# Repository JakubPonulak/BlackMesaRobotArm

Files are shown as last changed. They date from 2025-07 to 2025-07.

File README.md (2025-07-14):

<p align="center">
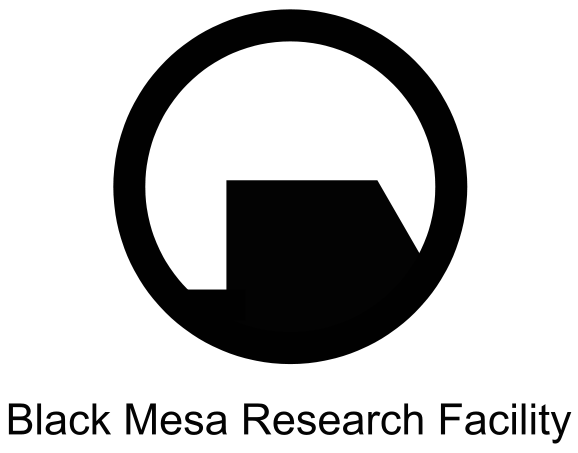
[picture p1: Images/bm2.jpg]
  
</p>

# Black Mesa Robot Arm
This is the GitHub repository for the Black Mesa Hazardous Material Manipulation Device, a small robot arm powered by an Arduino Uno microcontroller, which can be operated through keyboard inputs via Bluetooth. The purpose of this project was to utilize my knowledge of mechanical, electrical, and software engineering into a working device with a practical purpose.

<p align="center">
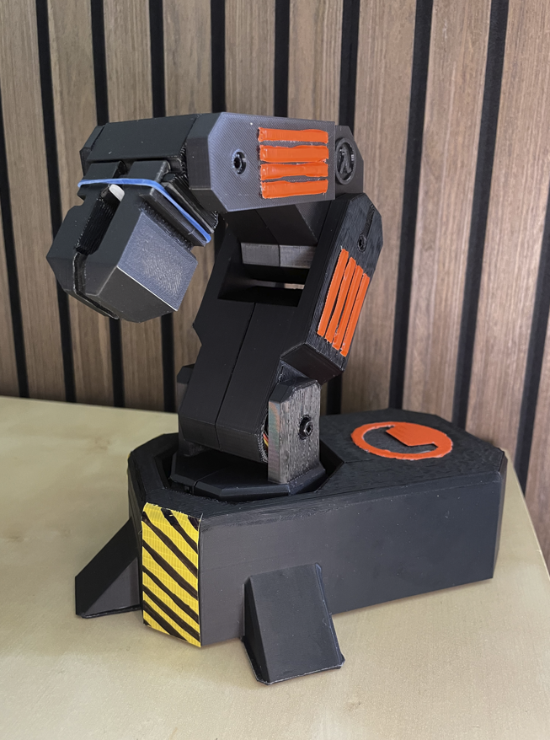
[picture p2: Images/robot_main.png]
  
</p>

The name of the robot, along with its design and decorative elements, come from the iconic video game "Half-Life", which was groundbreaking at the time of its release and has heavily impacted the FPS genre. Specifically, the robot name and design are a reference to the Black Mesa Research Facility, a fictional laboratory complex and research center which is the setting of the game. This game is a personal favorite of mine, and its aesthetic and theme fit perfectly into this project.

## Table of Contents

- [Initial Design](#initial-design)
- [Writing Code in Arduino Language and Python](#writing-code-in-arduino-language-and-python)
- [Final Assembly and Wiring](#final-assembly-and-wiring)
- [Do It Yourself!](#do-it-yourself)
- [Conclusion](#conclusion)

## Initial Design
I was first inspired to make this robot arm after watching [this video](https://www.youtube.com/watch?v=5toNqaGsGYs&list=PLPR41m1Dqd8Jqq6F-DI4-8zMKgnmrkHdz) by Build Some Stuff on YouTube. While the robot in the video was interesting on its own, I was determined to make my own version, both in terms of design and how it was to be controlled. I first got to work in Blender, a 3D modelling program that I have been using since high school, and I created a rough "sketch" of what I wanted my robot arm to look like:

<p align="center">
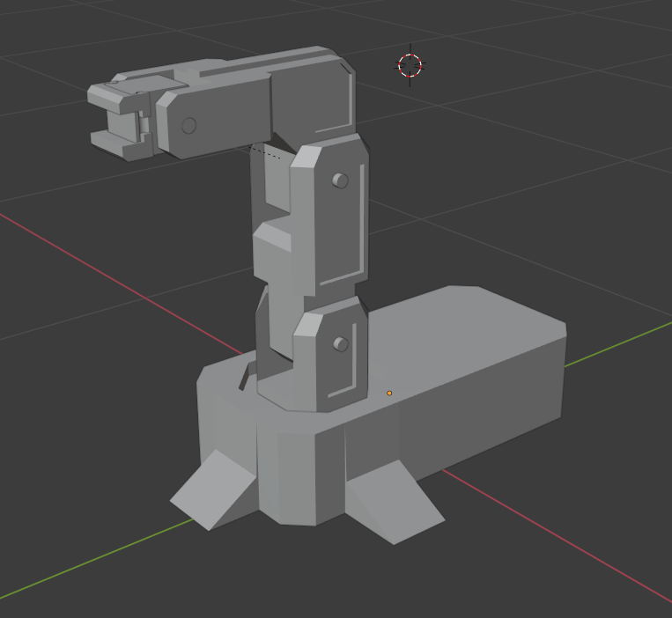
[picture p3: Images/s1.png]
  
</p>

After coming up with this design, I switched over to CAD modeling in SOLIDWORKS, which is better suited for creating real-life components, and with which I have much more experience. Based on dimensions given in the YouTube video's description, I was able to model each individual part of the robot and combine them into a complete SOLIDWORKS assembly, simulating the look and behavior of the robot arm. By importing additional pre-made parts such as Servo Motors and the Arduino Uno, I was able to ensure that the internal components of the robot would fit inside it, and that there were no interferences between components. 

DISCLAIMER: The assembly file that I have uploaded to this repository is a minimal version that can be built using only the parts I created. Please contact me if you would like a complete version that includes these additional parts.

<p align="center">
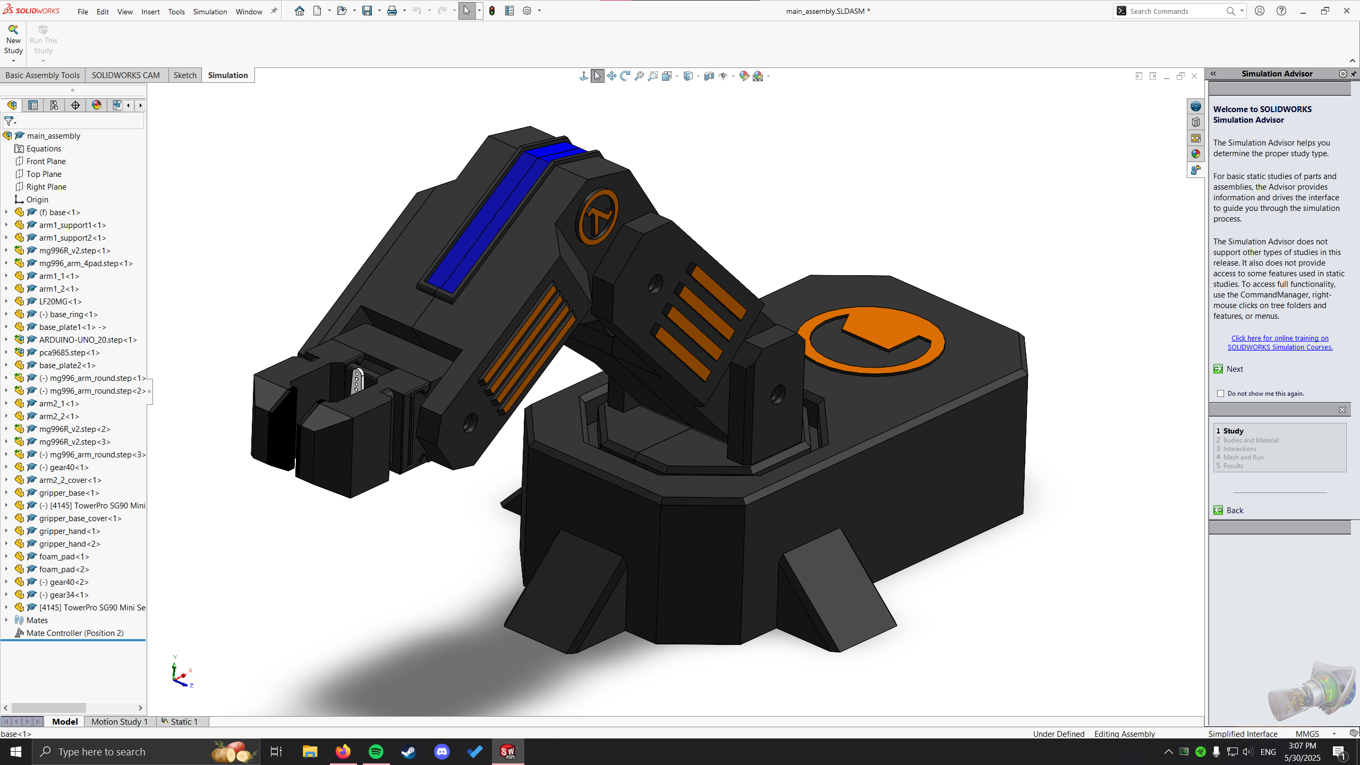
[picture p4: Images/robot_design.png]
  
</p>

Using SOLIDWORKS also allowed me to run an FEA simulation of the robot arm, specifically to see how the arm would react to a 300 gram object being held in place by the grippers, which is the maximum weight that I envisioned the robot would be able to carry with its limited grasp. I ran this simulation multiple times, varying the orientation of the arm in each run. The most critical iteration occurred when the arm was fully outstretched to the side, as this configuration exerted the greatest moment on the base.

<p align="center">
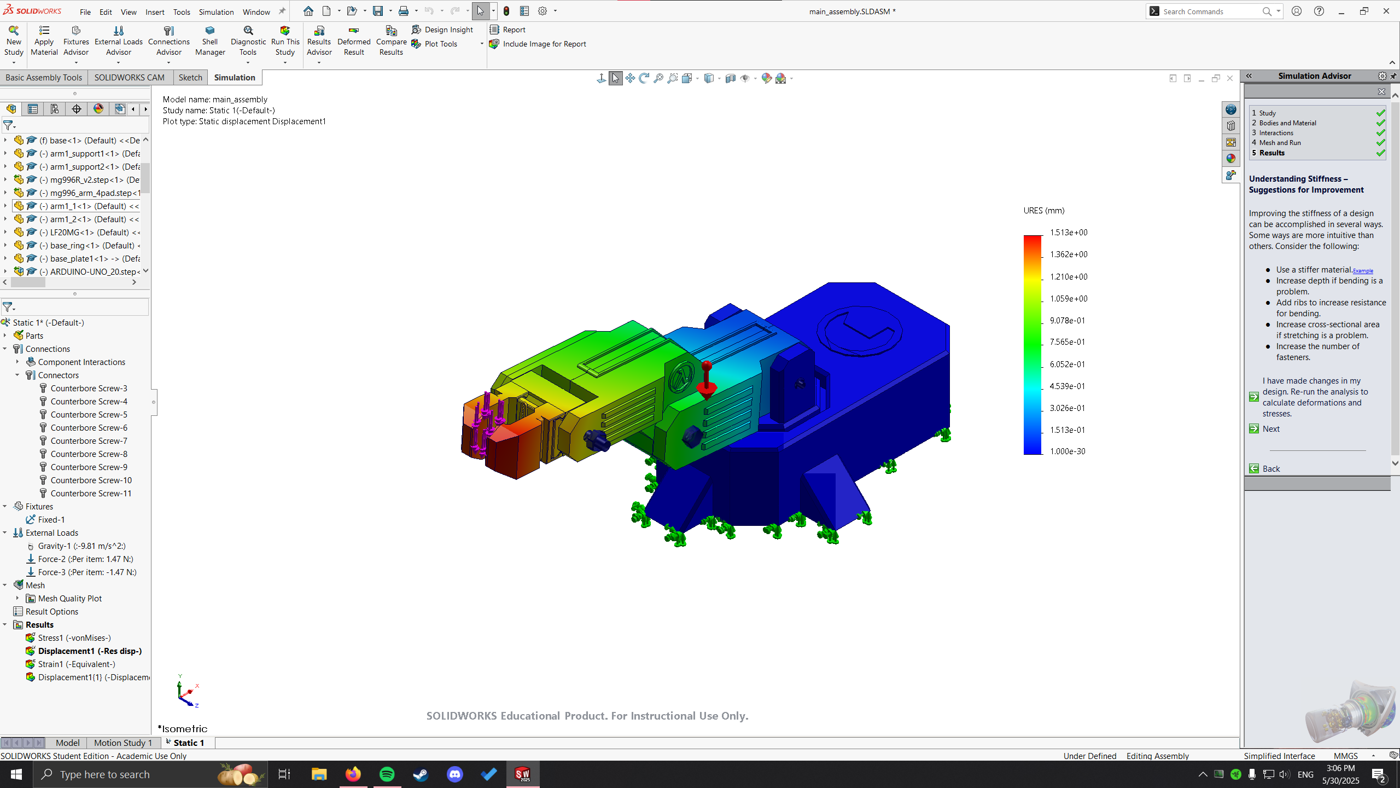
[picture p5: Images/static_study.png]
  
</p>

Once the design was complete, I uploaded my STP files to Craftcloud, an online 3D printing service that matches customers to manufacturers across the globe. While I waited for my parts to be printed in PLA and shipped to my home, I got to work on the software needed to run this robot arm.

## Writing Code in Arduino Language and Python
I had worked with Arduino boards and the Arduino language (a derivative of C++) in the past, and so I was already familiar with writing code for my microcontroller board. However, I had never worked with servo motors before, and so I had to learn about operating and manipulating them, which is where the Adafruit PWM Servo Driver Library comes in. This library allows easy manipulation of servo motors that are connected to the Arduino via a Servo Motor Driver board, which in my case was the PCA9685. I also utilized the EEPROM (Electrically Erasable Programmable Read-Only Memory) library, which allows the program to save data to the Arduino’s built-in non-volatile memory. This makes it possible to store servo positions or settings that are automatically restored when the robot is powered back on.

Initially, I thought that I would only need to write code in the Arduino IDE, but I soon realized that it did not allow for the type of user input I wanted. My initial plan was to control the robot using individual keystrokes like "A", "D", or "Space". However, the Arduino IDE lacked built-in functionality for detecting keyboard input. To work around this, I decided to use Python, which allowed me to use the _keyboard_ library, which allows scripts to detect and respond to keyboard input in real-time. The script reads the user's input on the keyboard, and sends a corresponding signal (a single integer or character) to the Arduino via the appropriate serial port. On the Arduino side, the uploaded code reads the incoming serial data and interprets the command by executing a predefined action, mainly changing the position of a specific servo motor. This setup allows real-time control of the robot arm through simple keystrokes on the keyboard.

## Final Assembly and Wiring
Once all of my 3D-printed parts and mechanical / electrical components arrived in the mail, I was ready to assemble the robot arm. Although the robot was designed with precision in SOLIDWORKS, the physical parts required several adjustments during assembly due to manufacturing imperfections. This included sanding down certain surfaces for a better fit, enlarging holes to properly accommodate screw diameters, and filing edges to improve joint mobility and rotation smoothness.

There were also some design flaws that I had failed to notice when first designing the parts for the robot arm. For example, some of the parts of the robot have cutouts for the servo motor wires, and I had underestimated how much space these wires would take up, especially at the base of the arm, where 4 sets of wires had to squeeze through a small opening. I ended up enlarging this cutout with a cordless drill, and I made sure to adjust the CAD file to match this adjustment if I was ever to reprint that specific part in the future. 

<p align="center">
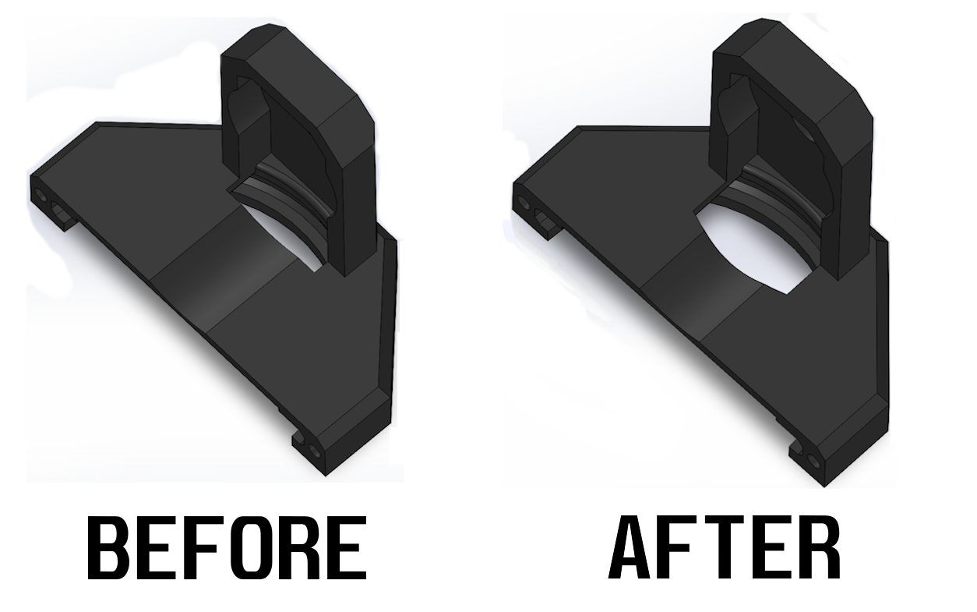
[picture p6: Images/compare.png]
  
</p>

Once the physical components were assembled, I moved on to wiring. I was fortunate to find online guides detailing how to wire the PCA9685 to the Arduino, as well as instructions for connecting the HC-05 Bluetooth module, which required a simple voltage divider that I assembled on a compact breadboard. However, during my first test, I encountered a major problem. Due to the limited space in the robot arm’s base, a short circuit occurred between the On/Off switch and the PCA9685 board. This short damaged the main ground wire and destroyed the female DC power adapter that connected the arm to my power supply. After a lot of troubleshooting and rewiring, I managed to resolve these issues, and the robot arm finally operated as intended. Below is a video of the robot arm in action (click the image to access the link).

<p align="center">
  <a href="https://drive.google.com/file/d/1IjUJEja0Yv61JHg0KjAD3Q2Ghb71W-9r/view?usp=sharing">
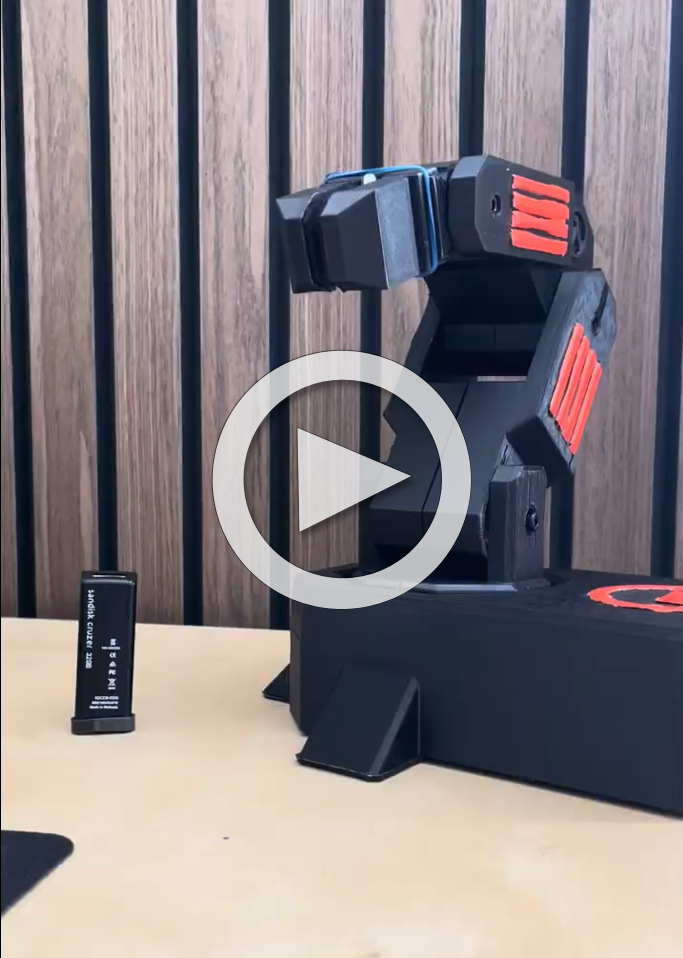
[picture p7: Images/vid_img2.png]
    
  </a>
</p>

## Do It Yourself!
One of the great things about this project is how easy it is to set up. All the necessary components can be ordered online, and the required software is free to download, except for SOLIDWORKS, which requires a paid subscription. However, there are great free alternatives, such as FreeCAD or Onshape. All the files provided in this repository are available for download, so you can use them as-is or modify them as a starting point for your own project. Below is a list of additional materials and parts you’ll need:

### Bill of Materials
#### Servos
- Main Servos: [Link](https://amzn.to/45xkgPH)
- 20KG Servo: [Link](https://amzn.to/43sGe4c)
- Micro Servo: [Link](https://amzn.to/3N3g3fj)
#### Electronics
- Arduino Board: [Link](https://amzn.to/3qfOmHg)
- Servo Driver Board: [Link](https://amzn.to/3spBGz1)
- HC-05 Bluetooth Module: [Link](https://www.amazon.com/Wireless-Bluetooth-Receiver-Transceiver-Transmitter/dp/B01MQKX7VP)
- Adjustable Power Supply: [Link](https://amzn.to/46e27Xa)
#### Hardware
- Screws Larger Set: [Link](https://amzn.to/3C47ASK)
- Screws Small Set: [Link](https://amzn.to/44GC2ih)
- Dupont Connector Kit: [Link](https://amzn.to/3qiVMth)
- T-Plugs: [Link](https://amzn.to/47df3g6)
- Wire/Shrink Wrap: [Link](https://amzn.to/3G3DEYU)
- Mini Breadboard Set: [Link](https://www.amazon.com/WWZMDiB-SYB-170-Breadboard-Plates-Multicolored/dp/B09YXQJMTG)
- Resistor Kit: [Link](https://www.amazon.com/Resistor-Resistors-Assortment-Breadboard-Electronics/dp/B0F4P352BB)
- USB-A Cable: [Link](https://www.amazon.com/dp/B00NH11KIK)
#### Other
- Gripper Gears: [Link](https://amzn.to/42eLIyz)
- Rubber Band: [Link](https://amzn.to/3so2O1n)
- Gripper Foam Pad: [Link](https://amzn.to/3SCE8wA)
- Power Switch: [Link](https://amzn.to/3und1LK)

Once you have all the components, 3D-printed parts, and the necessary code files downloaded, you’re ready to assemble and set up your own robot arm.

### Setup
1. Download the Arduino IDE and load robot_arm.ino: [Link](https://docs.arduino.cc/software/ide-v2/tutorials/getting-started/ide-v2-downloading-and-installing/)
2. Download and set up Python on your computer: [Link](https://www.python.org/downloads/)
3. Install the required Python libraries with this command: pip install pyserial keyboard
4. Follow the instructions in [these videos](https://www.youtube.com/watch?v=5toNqaGsGYs&list=PLPR41m1Dqd8Jqq6F-DI4-8zMKgnmrkHdz), made by the original creator Build Some Stuff on YouTube. Ignore the sections about the potentiometer controls.
5. Set up the HC-05 Bluetooth Module using the following wiring diagram:

<p align="center">
  
</p>

**Important Note**: Both the PCA9685 servo driver and the HC-05 Bluetooth module require a 5V power supply, and the Arduino Uno only has one 5V output pin. To power both modules at the same time, you’ll need to use a breadboard or a splitter to distribute the 5V line from the Arduino to both the PCA9685 and the HC-05. Be sure to also connect their grounds (GND) together with the Arduino’s GND to ensure a common reference voltage. 

5. Plug the USB-A cable into your robot and computer. This is how you will upload your code to the Arduino Uno itself.
6. Unplug the RX and TX wires (green and blue in the diagram) from the Arduino, as we cannot upload the code while they are connected.
7. Upload the Arduino code to the microcontroller in the Arduino IDE, then unplug the USB-A cable and reconnect the RX and TX wires.
8. Power on the robot by plugging in the T-Plug, setting your adjustable power supply to 6.0 V.
10. Pair the HC-05 Bluetooth module with your computer via Bluetooth. When prompted for a PIN, use the default code, which is typically 0000 or 1234.
11. Check what COM port the HC-05 is using in your computer's Device Manager, then update robot_arm.py to match it.
12. Run the robot_arm.py script and start controlling your robot arm with your keyboard!

## Conclusion
This project gave me the opportunity to apply my engineering knowledge in a practical setting while exposing me to real-world challenges that engineers face daily. It allowed me to develop my mechanical, electrical, and software skills in a hands-on and rewarding way. I highly recommend this type of project to anyone passionate about Mechanical Engineering who wants to gain valuable, multidisciplinary experience.

This project is licensed under the MIT License, which allows anyone to use, modify, and share the content, provided they give proper credit to the original author.

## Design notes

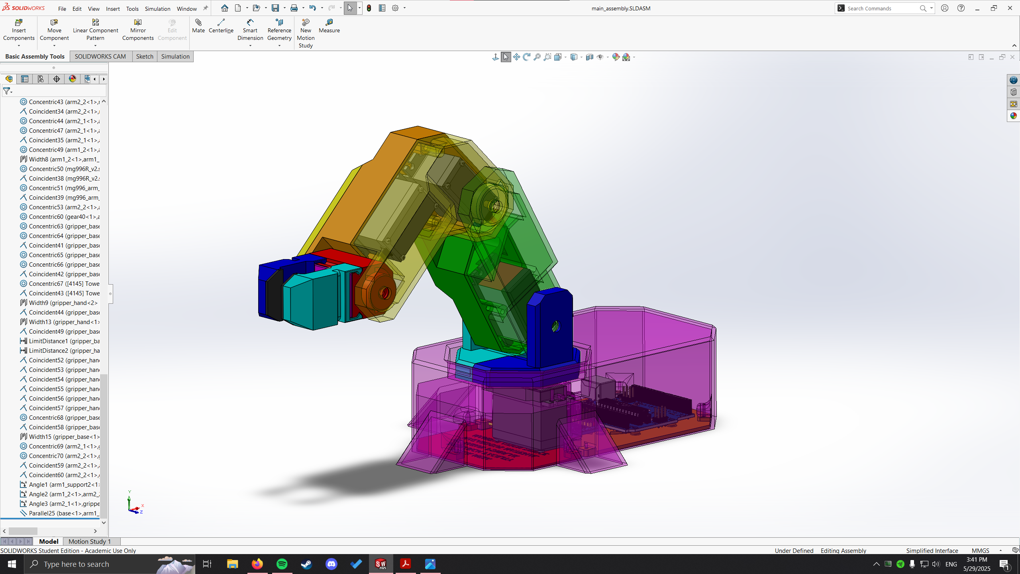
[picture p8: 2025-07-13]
Images/robot_complete.png

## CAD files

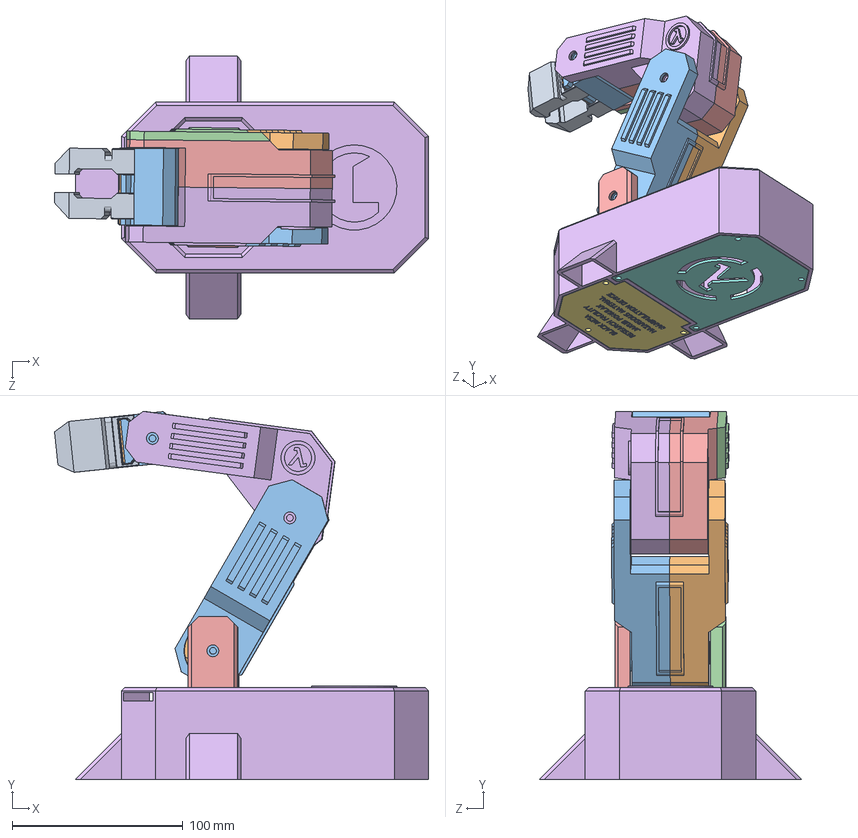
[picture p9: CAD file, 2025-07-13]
CAD Files/main_assembly_min.SLDASM
219.2 x 215.8 x 154.0 mm
base
arm1_support1
arm1_support2
arm1_1
arm1_2
base_ring
base_plate1
base_plate2
arm2_1
arm2_2
arm2_2_cover
gripper_base
gripper_base_cover
gripper_hand x 2

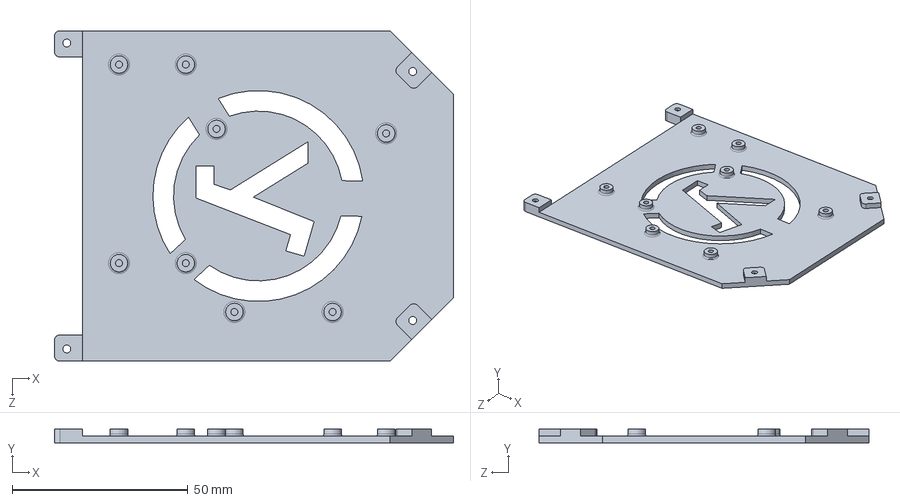
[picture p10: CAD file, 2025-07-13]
CAD Files/base_plate1.SLDPRT
113.5 x 4.00 x 94.0 mm

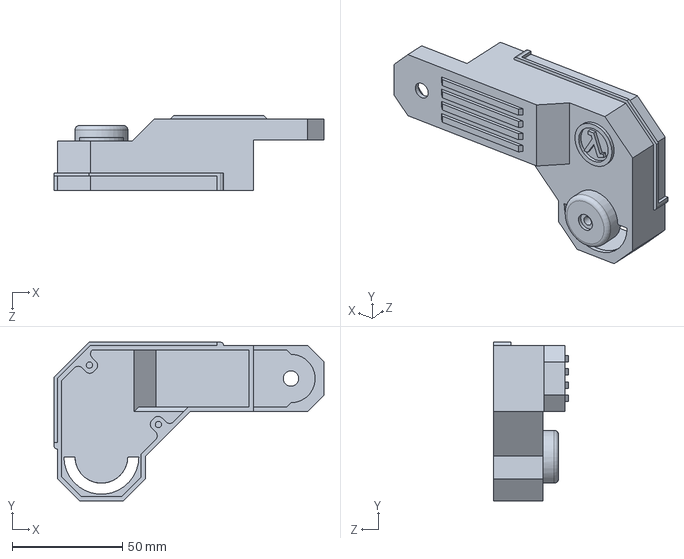
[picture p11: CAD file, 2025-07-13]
CAD Files/arm2_1.SLDPRT
122.5 x 72.0 x 34.0 mm

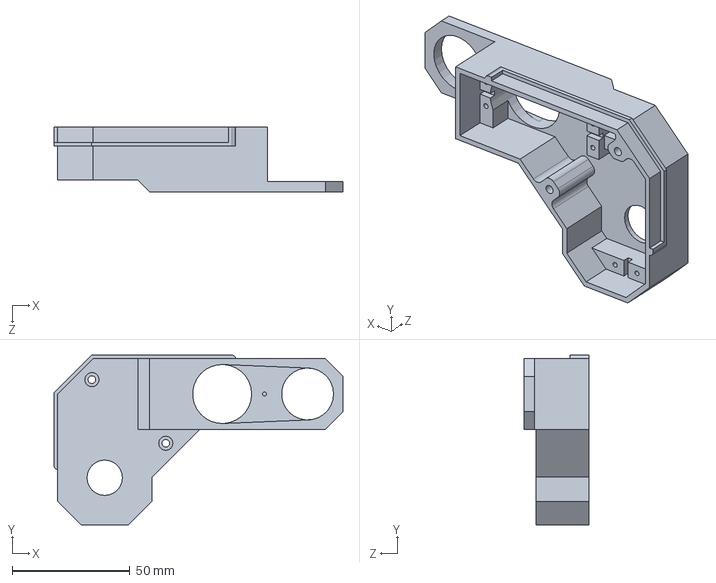
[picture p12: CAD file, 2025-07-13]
CAD Files/arm2_2.SLDPRT
122.5 x 72.0 x 27.5 mm

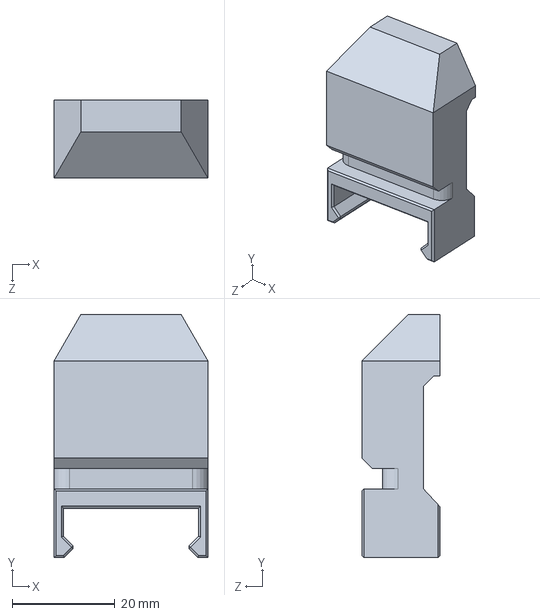
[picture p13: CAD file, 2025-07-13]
CAD Files/gripper_hand.SLDPRT
30.0 x 47.4 x 15.2 mm

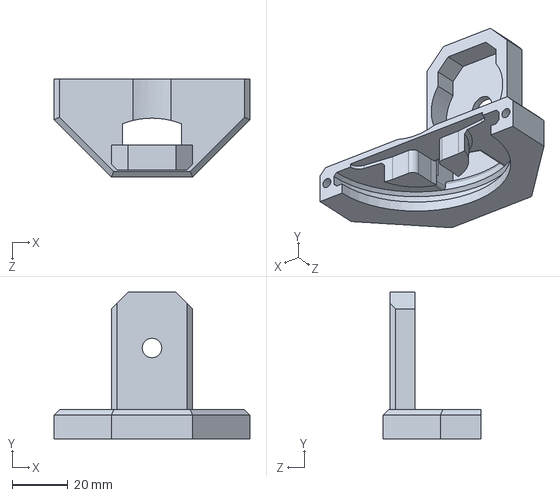
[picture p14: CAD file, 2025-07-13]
CAD Files/arm1_support1.SLDPRT
70.0 x 52.5 x 35.0 mm

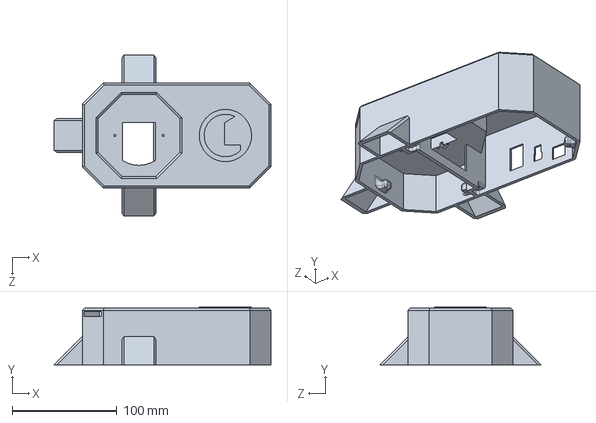
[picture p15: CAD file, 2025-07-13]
CAD Files/base.SLDPRT
207.0 x 55.0 x 154.0 mm

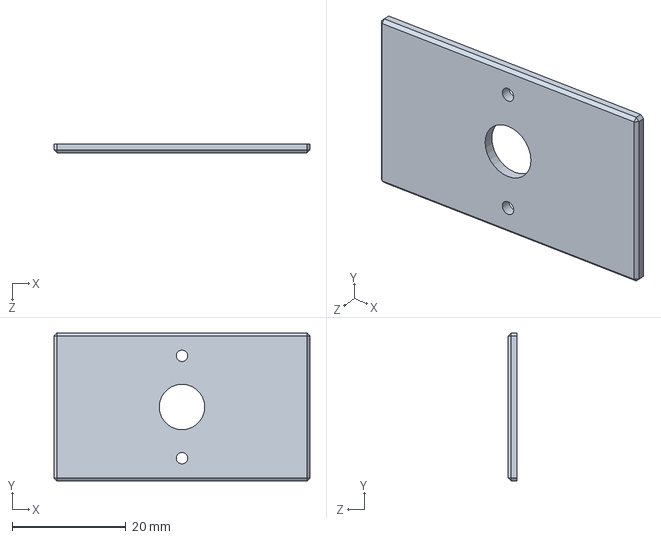
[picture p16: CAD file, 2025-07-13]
CAD Files/gripper_base_cover.SLDPRT
45.0 x 26.0 x 1.50 mm

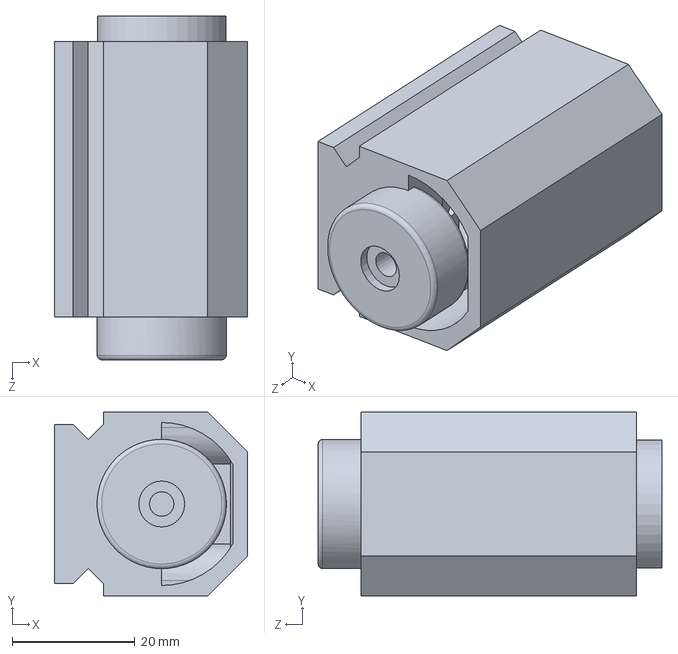
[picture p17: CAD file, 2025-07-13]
CAD Files/gripper_base.SLDPRT
31.5 x 30.0 x 56.1 mm

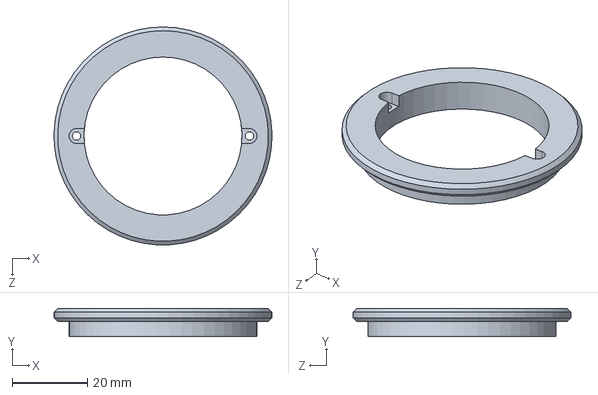
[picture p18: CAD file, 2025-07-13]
CAD Files/base_ring.SLDPRT
58.0 x 7.50 x 58.0 mm

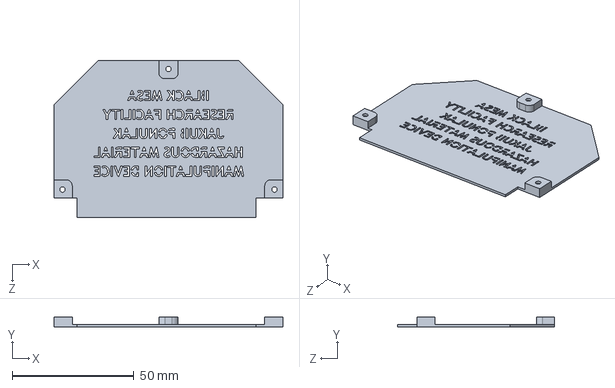
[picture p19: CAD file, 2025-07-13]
CAD Files/base_plate2.SLDPRT
94.0 x 4.00 x 64.5 mm

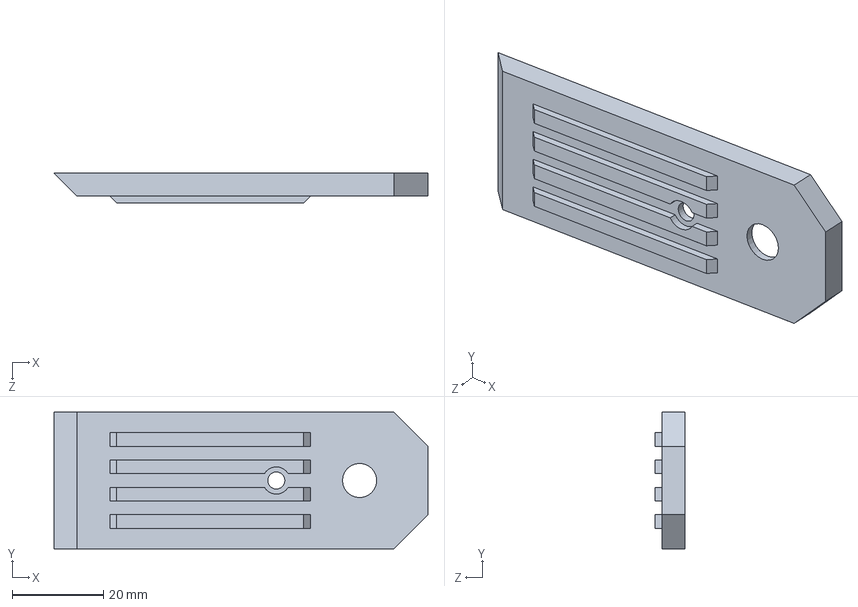
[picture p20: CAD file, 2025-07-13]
CAD Files/arm2_2_cover.SLDPRT
82.0 x 30.0 x 6.50 mm

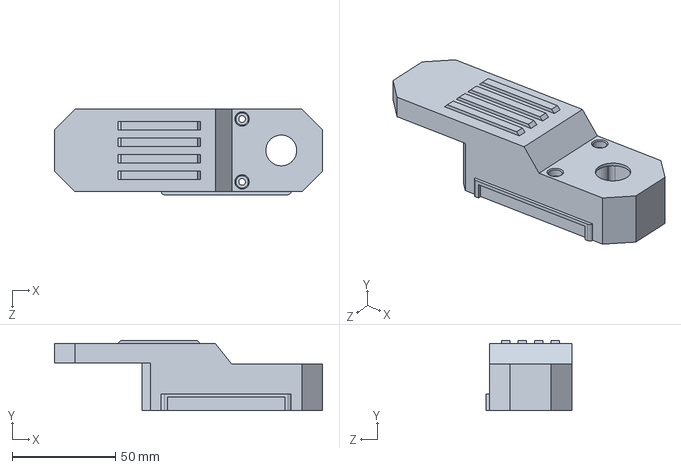
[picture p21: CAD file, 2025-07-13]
CAD Files/arm1_2.SLDPRT
130.0 x 34.0 x 41.5 mm

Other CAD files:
CAD Files/arm1_support2.SLDPRT
CAD Files/arm1_1.SLDPRT

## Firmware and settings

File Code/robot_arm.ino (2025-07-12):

#include <Wire.h>
#include <EEPROM.h>
#include <Adafruit_PWMServoDriver.h>

#define servoMin 75
#define servoMax 535
#define handMin 305
#define handMax 415

Adafruit_PWMServoDriver pwm = Adafruit_PWMServoDriver();  // REMEMBER TO SET VOLTAGE TO 6.00 V

int hand = 11;
int wrist = 10;
int elbow = 9;  //Assign Motors to pins on Servo Driver Board
int shoulder = 7;
int base = 5;

int pos1 = 305;  // hand
int pos2 = 305;  // wrist
int pos3 = 305;  // elbow                // 305 is intermediate value, "middle" of servo
int pos4 = 305;  // shoulder
int pos5 = 305;  // base

const int step = 5;  // step for servo movement per keypress

void setup() {
  Serial.begin(9600);
  pwm.begin();
  pwm.setPWMFreq(50);  // set frequency to 50 Hz
  EEPROM.get(0, pos1);
  EEPROM.get(2, pos2);
  EEPROM.get(4, pos3);
  EEPROM.get(6, pos4);
  EEPROM.get(8, pos5);
  pwm.setPWM(hand, 0, pos1);
  pwm.setPWM(wrist, 0, pos2);
  pwm.setPWM(elbow, 0, pos3);
  pwm.setPWM(shoulder, 0, pos4);
  pwm.setPWM(base, 0, pos5);
}

void loop() {
  if (Serial.available() > 0) {
    char cmd = Serial.read();
    // hand movement
    if (cmd == '4') {
      pos1 += step;
      if (pos1 > handMax) pos1 = handMax;
      pwm.setPWM(hand, 0, pos1);
      Serial.print("Hand opening. Position: ");
      Serial.println(pos1);
    } else if (cmd == '5') {
      pos1 -= step;
      if (pos1 < handMin) pos1 = handMin;
      pwm.setPWM(hand, 0, pos1);
      Serial.print("Hand closing. Position: ");
      Serial.println(pos1);
    }
    // wrist movement
    else if (cmd == '6') {
      pos2 += step;
      if (pos2 > servoMax - 35) pos2 = servoMax - 35;
      pwm.setPWM(wrist, 0, pos2);
      Serial.print("Wrist moving up. Position: ");
      Serial.println(pos2);
    } else if (cmd == '7') {
      pos2 -= step;
      if (pos2 < servoMin + 35) pos2 = servoMin + 35;
      pwm.setPWM(wrist, 0, pos2);
      Serial.print("Wrist moving down. Position: ");
      Serial.println(pos2);
    }
    // elbow movement
    else if (cmd == '8') {
      pos3 += step;
      if (pos3 > servoMax) pos3 = servoMax;
      pwm.setPWM(elbow, 0, pos3);
      Serial.print("Elbow moving down. Position: ");
      Serial.println(pos3);
    } else if (cmd == '9') {
      pos3 -= step;
      if (pos3 < servoMin) pos3 = servoMin;
      pwm.setPWM(elbow, 0, pos3);
      Serial.print("Elbow moving up. Position: ");
      Serial.println(pos3);
    }
    // shoulder movement
    else if (cmd == '3') {
      pos4 += step;
      if (pos4 > servoMax) pos4 = servoMax;
      pwm.setPWM(shoulder, 0, pos4);
      Serial.print("Shoulder moving down. Position: ");
      Serial.println(pos4);
    } else if (cmd == '2') {
      pos4 -= step;
      if (pos4 < servoMin) pos4 = servoMin;
      pwm.setPWM(shoulder, 0, pos4);
      Serial.print("Shoulder moving up. Position: ");
      Serial.println(pos4);
    }
    // base movement
    else if (cmd == '0') {
      pos5 += step;
      if (pos5 > servoMax) pos5 = servoMax;
      pwm.setPWM(base, 0, pos5);
      Serial.print("Base moving left. Position: ");
      Serial.println(pos5);
    } else if (cmd == '1') {
      pos5 -= step;
      if (pos5 < servoMin) pos5 = servoMin;
      pwm.setPWM(base, 0, pos5);
      Serial.print("Base moving right. Position: ");
      Serial.println(pos5);
    }
    // saving location
    else if (cmd == 's') {
      EEPROM.put(0, pos1);
      EEPROM.put(2, pos2);
      EEPROM.put(4, pos3);
      EEPROM.put(6, pos4);
      EEPROM.put(8, pos5);
    }
  }
}

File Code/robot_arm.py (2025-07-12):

import serial
import keyboard
import time
import os

arduino = serial.Serial('COM10', 9600)
# Replace COM10 with the port the HC05 is using

keys = ['a','d','w','s','space','ctrl','q','e','z','c']
# List of keys that correspond to commands

print("Ready to Recieve Commands:")
print("Commands:")
print("Gripper Open/Close: Space/Ctrl")
print("Wrist Up/Down: Q/E")
print("Elbow Up/Down: Z/C")
print("Shoulder Up/Down: W/S")
print("Base Left/Right: A/D")

while True:
    if arduino.in_waiting > 0:
        line = arduino.readline().decode('utf-8').rstrip()
        if line:
            print("From Arduino:", line)

    for i, key in enumerate(keys):
            if keyboard.is_pressed(key):
                arduino.write(f"b{i}".encode())
                time.sleep(0.001)
                
    if keyboard.is_pressed('`'):
        print("Stopping script...")
        arduino.write("s".encode())
        time.sleep(1)
        os.system('cls')
        break    

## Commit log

2025-07-13 Rename arm1_1.SLDPRT to CAD Files/arm1_1.SLDPRT
    [arm1_1.SLDPRT]
2025-07-13 Rename arm1_2.SLDPRT to CAD Files/arm1_2.SLDPRT
    [arm1_2.SLDPRT]
2025-07-13 Rename arm1_support1.SLDPRT to CAD Files/arm1_support1.SLDPRT
    [arm1_support1.SLDPRT]
2025-07-13 Rename arm1_support2.SLDPRT to CAD Files/arm1_support2.SLDPRT
    [arm1_support2.SLDPRT]
2025-07-13 Rename arm2_1.SLDPRT to CAD Files/arm2_1.SLDPRT
    [arm2_1.SLDPRT]
2025-07-13 Rename arm2_2.SLDPRT to CAD Files/arm2_2.SLDPRT
    [arm2_2.SLDPRT]
2025-07-13 Rename arm2_2_cover.SLDPRT to CAD Files/arm2_2_cover.SLDPRT
    [arm2_2_cover.SLDPRT]
2025-07-13 Rename base.SLDPRT to CAD Files/base.SLDPRT
    [base.SLDPRT]
2025-07-13 Rename base_plate1.SLDPRT to CAD Files/base_plate1.SLDPRT
    [base_plate1.SLDPRT]
2025-07-13 Rename base_plate2.SLDPRT to CAD Files/base_plate2.SLDPRT
    [base_plate2.SLDPRT]
2025-07-13 Rename base_ring.SLDPRT to CAD Files/base_ring.SLDPRT
    [base_ring.SLDPRT]
2025-07-13 Rename gripper_base.SLDPRT to CAD Files/gripper_base.SLDPRT
    [gripper_base.SLDPRT]
2025-07-13 Rename gripper_base_cover.SLDPRT to CAD Files/gripper_base_cover.SLDPRT
    [gripper_base_cover.SLDPRT]
2025-07-13 Rename gripper_hand.SLDPRT to CAD Files/gripper_hand.SLDPRT
    [gripper_hand.SLDPRT]
2025-07-13 Rename main_assembly_min.SLDASM to CAD Files/main_assembly_min.SLDASM
    [main_assembly_min.SLDASM]
